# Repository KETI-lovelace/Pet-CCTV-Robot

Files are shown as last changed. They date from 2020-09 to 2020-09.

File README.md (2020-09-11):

# Pet-CCTV-Robot
2020 제4회 KETI 모비우스 개발자 대회 러브레이스 팀

## Overview
  직장인들의 외출에 펫을 감시하기 위한 펫 CCTV, 하지만 기존 펫 CCTV는 사용자가 앱으로 직접 스트리밍 영상을 보면서 반려동물의 상황을 파악 해야하기 때문에 용무가 있어 외출을 한 사용자들에게는 스트리밍 영상을 통한 감시를 할 수 없는 상황이 대부분이다. 또한, 터치를 통해 구동되는 가전제품들이 증가함으로 반려동물의 사고 또한 빈번히 발생한다. 예로 반려동물 주인이 외출시 반려동물이 인덕션, 하이라이트 전자레인지 등을 건드려서 화재가 발생했다는 사건이 급증했다. ([화재사건기사내용](https://www.hankyung.com/life/article/201912041776Y)) 우리는 이에대해 기존의 제품이 구매자의 목적을 완벽하게 해소시켜주지 못한다는 점과 현재 사고들의 원인을 파악하여 사용자가 위험구역을 지정하고, 반려동물의 위치를 자동적으로 파악하여 기존 펫 CCTV의 부족한 점을 보완하고자한다.
 
## 세부 기능
- 사용자가 직접 본 기기 카메라에서 송출하는 화면을 통해 전면, 좌측, 우측 방향에 반려동물이 접근하면 안되는 구역을 설정을 할 수 있다.
- 본 기기는 인공지능을 통해 전면, 좌측, 우측 방향으로 반려동물의 위치를 파악한다.
- 반려동물이 사용자가 지정한 접근 금지 구역에 위치했을 때 기기는 음성을 송출하여 반려동물에게 제지를 하고, 사용자의 앱에 알림을 울린다. ([소리를 통해 반려동물을 제지할 수 있을까?](https://youtu.be/sFJ1QNv7OGw?t=42))

## 순차적 동작 개념 설명
1.	카메라에서 송출하고 있는 영상이 터치 스크린에 출력이 되고, 모터를 통해 움직이는 카메라의 각도(0도, 90도, 180도)별로 원하는 위험구역을 스크린에 터치한다.
2.	위험 구역 설정을 마무리하면, 카메라에서 촬영되고 있는 영상을 앱에 실시간으로 전송한다.
3.	6초 간격으로 모터를 돌려 카메라의 위치를 바꾼다. (이때 해당 카메라 각도로 설정한 위험구역을 불러온다.)
4.	고양이 / 강아지를 탐지한다.
5.	탐지한 고양이/ 강아지의 위치가 사용자가 설정한 위험구역 내에 위치할 경우 스피커로 음성 송출 및 사용자 앱에 알림을 송신한다.

## 사용재료
  라즈베리 파이3B+, 라즈베리 파이4, 라즈베리파이 카메라 모듈*2, 180도 서보모터, 마이크로 SD카드 32G, SD카드 리더기, 라즈베리파이 공식7인치 터치스크린, 스피커 모듈, Coral USB accelerator

## 모델링 

모델은 [STL 파일](https://github.com/KETI-lovelace/Pet-CCTV-Robot/tree/master/hard%20case)로 첨부한다. 3D프린팅 편의를 위해 파트가 다음과 같이 분할되어 있다. 

```
hard case
 ├─camera_fixer.STL
 ├─camera_fixer_front.STL
 ├─cat_ear2.STL
 ├─cat_head_case.STL
 ├─cat_neck3.STL
 ├─cat_shape_behind2.STL
 ├─cat_shape_cap4.STL
 ├─cat_shape_side_wall3_back.STL
 ├─cat_shape_side_wall3_front.STL
 ├─head_behind.STL
 └─motor_case3.STL
```

위의 파트들을 모두 합쳐 에셈블을 만들면 다음과 같다.
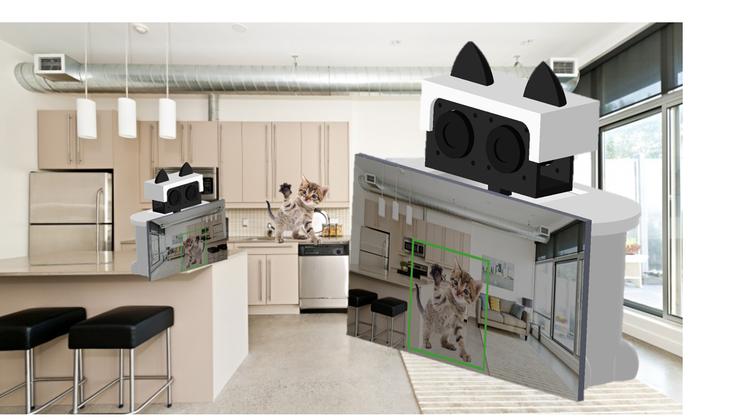
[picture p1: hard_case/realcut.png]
최종 모델


## 하드웨어 세부 구성
```
.
├── Google Edge TPU coprocessor : 인공지능 영상처리 가속화
├── raspberry pi 3 B+: 사용자에게 영상을 스트리밍 해줄 보드 
├── raspberry pi 4: 애완동물을 인식하여 위험구역을 탐지할 보드
├── HS-311 servo motor: 카메라를 돌려줄 모터
├── SONY pi camera x 2: 카메라(하나는 애완동물 인식, 하나는 스트리밍용)
├── raspberry pi touch screen 7 inch: 사용자가 상호작용할 터치디스플레이
└── USB port speaker: 음성을 출력할 스피커
```

## 반려동물 감지 (detection)
파이카메라로 받은 영상을 Tensorflow-Lite와 OpenCV, Google의  sample TFLite model을 이용하여 고양이, 강아지, 새 등의 애완동물을 인공지능으로 학습하여 인식 가능하게 만들었다. 파이카메라로 영상을 받으면, 처음에 터치스크린을 터치하여 화면 상의 위험 구역을 선정한다. 그러면 화면 상에 고양이, 강아지 등 반려동물이 보이면 인공지능이 인식을 하고, 사용자가 선정한 위험 구역 범위에 인식된 반려동물의 좌표값이 들어오면 반려동물의 행위를 저지하는 음성을 출력하고, 사용자의 앱으로 알림을 준다. 영상처리에서는 FPS를 개선하기 위해 TPU Accelerator를 사용하였으며, raspberry pi 3 B 에서 raspberry pi 4로 새로 교체하여 기존의 파이카메라로 영상처리를 할때 약 1에서 2 FPS였던 것을 약 30에서 40 FPS정도까지 끌어올려 부드러운 영상이 나오도록 했다. 
파일 실행 방법은 다음과 같다.
```
source tflite1-env/bin/activate
python3 TFLite_detection_webcam.py --modeldir=Sample_TFLite_model --edgetpu
```
## 애플리케이션
앱으로도 카메라의 영상이 스트리밍 될 수 있도록 하기 위해 UV4L/AWS를 사용하여 영상이 스트리밍 될 수 있도록 두가지 버전을 만들었다. UV4L을 이용할 경우, 스트리밍 하는 영상의 width, height, brightness, contrast, saturation, rgb balance, sharpness, rotate, jpeg quality, frame rate, horizontal mirror, vertical mirror, video denoise, image stabilization 등등 다양한 설정값을 변경하여 영상 스트리밍을 앱으로 받아볼 수 있다. <br>
### 주의사항
1. UV4L을 사용할 경우 : 라즈베리파이와 앱이 설치된 핸드폰이 반드시 같은 와이파이를 사용하고 있어야 영상 스트리밍 가능. 스트리밍 딜레이 거의 없음.
2. AWS를 사용할 경우 : 라즈베리파이와 앱이 설치된 핸드폰이 와이파이 사용 종류에 구애받지 않음. 인터넷 환경에 따라 스트리밍에서 1~10초의 딜레이 발생.

라즈베리 파이에서 인공지능으로 고양이, 강아지를 인식하여 사용자가 지정한 위험구역에 들어오면 앱으로 푸시알림을 보낸다. 사용자가 이름과 email 정보를 입력하면 반려동물이 위험구역에 접근했을 때 앱으로 알림이 가는 서비스를 구독할 수 있다. 구독자의 정보는 파이어베이스 데이터베이스에 실시간으로 반영되고, 구독 해지 시 자동으로 데이터베이스에서 정보를 삭제한다. 파이어베이스에서 사용자들의 정보와 사용량, 동시 연결 수, 클라우드 메시징(푸시알림)이 사용자에게 몇번 전송되고, 수신되고, 노출되고, 열렸는지를 실시간으로 모니터링할 수 있다. 또한 여러 대의 스마트폰 디바이스에서 실시간 스트리밍을 볼 수 있고, 푸시알림을 받을 수 있다.

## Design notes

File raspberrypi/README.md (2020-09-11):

# 라즈베리파이 내 프로그램 상세 설명

## 프로그램 세부 구성

1. [위험 구역 설정](https://github.com/KETI-lovelace/Pet-CCTV-Robot/tree/master/raspberrypi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)
2. [모터 회전](https://github.com/KETI-lovelace/Pet-CCTV-Robot/tree/master/raspberrypi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)
3. [반려동물 디텍팅](https://github.com/KETI-lovelace/Pet-CCTV-Robot/tree/master/raspberrypi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)
4. [소리 송출](https://github.com/KETI-lovelace/Pet-CCTV-Robot/tree/master/raspberrypi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)

## 1. 위험 구역 설정



### 코드부분
```python
while True:
    danger_frame = videostream.read()
    cv2.rectangle(danger_frame,(440,370),(540,410),(255,255,255),-1)
    cv2.putText(danger_frame,'NEXT'.format(frame_rate_calc),(450,400),cv2.FONT_HERSHEY_SIMPLEX,1,(50,50,255),2,cv2.LINE_AA)
    cv2.namedWindow('set_danger',cv2.WND_PROP_FULLSCREEN)
    cv2.setWindowProperty('set_danger',cv2.WND_PROP_FULLSCREEN,cv2.WINDOW_FULLSCREEN)
    cv2.imshow('set_danger', danger_frame)
    cv2.setMouseCallback('set_danger', mouse_callback)
    if(next_btn >  2): # 모든 위험구역 설정 완료
        next_btn = 2
        break
    k = cv2.waitKey(1)
    if k == 'd':
        break
cv2.destroyAllWindows()
```

### 상세 설명
- 좌측에서부터 카메라로부터 촬영되는 화면을 스크린을 통해 볼 수 있다.
- ``mousecallback`` 함수를 이용해 원하는 위험구역을 설정을 완료하고 ``NEXT`` 버튼을 누른다.
- 모터가 움직이며 우측,정면에서도 동일한 과정을 거친다.

## 2. 모터 구동

### 코드 부분

```python
# next_btn = 0 : 0 angle , = 1 : 90 angle , 2 = 180 angle

# motor angle change
pi = pigpio.pi()
pi.set_servo_pulsewidth(servoPin, 0) # turn off 18 pin connected servo motor.
pi.set_servo_pulsewidth(servoPin,800 * next_btn + 700)

# automatically change servomotor angle
while True:
    count += 1
    if( count > 180 ) :
        count = 0
        pi.set_servo_pulsewidth(servoPin,800 * next_btn + 700)
        if(is180):
            curr_btn = next_btn
            next_btn -= 1
        else:
            curr_btn = next_btn
            next_btn += 1
        if(next_btn == 2 or next_btn  == 0):
            is180 = not is180

...

```
### 상세 설명

- ``pigpio`` 모듈 사용
    - 원래는 ``ChangeDutyCycle`` 를 이용해 모터 각도를 전환시켰으나 떨림이 심해서, ``pigpio``선택
    - 설치 방법은 아래와 같다.

    ```bash
    $sudo apt-get update
    $sudo apt-get install pigpio python-pigpio python3-pigpio
    ```
    - 코드 작성 방법은 아래와 같다.

    ```python
    import pigpio

    from time import sleep
    
    pi = pigpio.pi() #먼저 사용할 pigpio.pi를 매칭해줍니다.
    while True:
        pi.set_servo_pulsewidth(18, 0) # 18번 채널에연결된 서보모터를 꺼줍니다. 
        sleep(1)
        pi.set_servo_pulsewidth(18, 700) # 18번채널에 연결된 서보모터를 0도로 이동
        sleep(1)
        pi.set_servo_pulsewidth(18, 1500) # 가운데로 이동 90도
        sleep(1)
        pi.set_servo_pulsewidth(18, 2300) # 180도 끝으로 이동. 
        sleep(1)
    ```
    - 실행 방법은 아래와 같다.

    ```bash
    $sudo pigpiod # pigpiod 실행
    $sudo python3 [파일 명]
    $sudo killall pigpiod # pigpiod 종료
    ```
- ``next_btn`` 이 0,1,2 일 때, 각각 0도, 90도 180도 표지를 의미한다.
- ``count``가 180 이상이되면, 모터 각도를 0도 -> 90도 -> 180도 -> 90도 -> 0도 순서대로 전환하는것을 반복한다.

## 3. 반려동물 디텍팅



- 라즈베리파이 반려동물 디텍팅에는 다음의 [오픈소스](https://github.com/EdjeElectronics/TensorFlow-Lite-Object-Detection-on-Android-and-Raspberry-Pi/blob/master/Raspberry_Pi_Guide.md)를 이용했다.

## 4. 소리 송출

### 코드 부분

```python
pygame.mixer.init()
music_file = "Dontgo.wav"
pygame.mixer.music.load(music_file)
pygame.mixer.music.play()
clock=pygame.time.Clock()
while pygame.mixer.music.get_busy():
    clock.tick(5)
```

### 상세 설명

- ``pygame`` 모듈 이용

## 5. 안드로이드 앱
Firebase로 안드로이드 앱에 알림을 보내는 부분으로, appalarm.py이다.<br>

### 코드 부분
```python
#3. 먼저 firebase database에서 저장된 token을 모두 가져와야 한다.
firebase = firebase.FirebaseApplication("https://soboro-6d610.firebaseio.com/", None)
result = firebase.get("/users", None)
listToken = []
for k, v in result.items():
    listToken.append(v["token"])
```
```python
push_service = FCMNotification(api_key="AAAACXndXcs:APA91bETtBU2UsGeSIToJYp4SFfx0VimIQthlDvZDQD5MmDAD0dCIqbl2JOevt0O0thLAJAGNb_rxkQzeuUYF51CkqO8O0Q_HVtP84TrrTnjE8nnuLJOLXHAHdsUepMfKH2szyw8YklQ")
```
이 부분에 본인의 FCMNotification api key를 입력한다. 확인 방법은 다음과 같다.<br>
Firebase 콘솔 접속 -> Settings -> 클라우드 메시징 -> 서버 키 부분의 토큰<br>
```python
message_title = "Soboro"
message_body = "Hurry up! Your pet is danger! Click this alarm!"
message_sound = "default"
```
이부분을 수정하여 푸시 알림의 타이틀, 내용, 소리 등을 바꿀 수 있다.<br>
<br>
appalarm.py는 TFLite_detection_webcam.py에서 쉡스크립트로 실행된다.<br>
```python
subprocess.call(['bash', 'runappalarm.sh'])
```
### 실행 전 설치 라이브러리
```
$sudo pip install pyfcm
```

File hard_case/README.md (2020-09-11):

## 하드케이스 모델링

### 연출 사진



### 구성

```
hard case
 ├─camera_fixer.STL
 ├─camera_fixer_front.STL
 ├─cat_ear2.STL
 ├─cat_head_case.STL
 ├─cat_neck3.STL
 ├─cat_shape_behind2.STL
 ├─cat_shape_cap4.STL
 ├─cat_shape_side_wall3_back.STL
 ├─cat_shape_side_wall3_front.STL
 ├─head_behind.STL
 └─motor_case3.STL
```

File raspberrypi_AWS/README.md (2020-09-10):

# AWS를 이용한 영상 스트리밍 상세 설명
이 파일을 영상 스트리밍을 할 라즈베리파이에 다운받고 AWS 스트리밍을 위해 다음과 같은 작업을 해줍니다.<br>
<br>

## 라즈베리파이에서 수행해줘야 할 작업
라즈베리파이에서 AWS 스트리밍을 실행하기 위해서는 이 레포지토리의 raspberrypi_AWS 폴더를 다운받은 뒤 다음과 같은 절차를 따릅니다.<br>
```
1. 라이브러리 설치
$ sudo apt-get install libgstreamer1.0-dev libgstreamer-plugins-base1.0-dev gstreamer1.0-plugins-base-apps gstreamer1.0-plugins-bad gstreamer1.0-plugins-good gstreamer1.0-plugins-ugly gstreamer1.0-tools

2. 환경변수 설정
$ export AWS_ACCESS_KEY_ID=YourAccessKeyId
$ export AWS_SECRET_ACCESS_KEY=YourSecretAccessKey

3. 종속 라이브러리 연결
$ cd /etc/ld.so.conf.d
$ sudo vim kinesis.conf
실행 파일이랑 같이 넘겨준 libKinesisProducer.so 등이 저장되어 있는 경로 입력
$ sudo ldconfig

4. 실행
$./KinesisStreaming.out <streaming name>
```
<br>
streaming name은 App_AWS에서 설정되어있는 arten입니다. 변경하려면 직접 안드로이드 스튜디오에서 코드를 수정하세요.

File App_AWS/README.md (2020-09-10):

# AWS를 이용한 영상 스트리밍 Android App 상세 설명
라즈베리파이에서 위험 구역에 반려 동물 진입 시 사용자 앱으로 알림을 전송합니다.<br>
앱 알림은 Firebase로 구현되어 있습니다.<br>
실시간 스트리밍 기능은 AWS로 구현되어 있습니다.<br>
이 앱을 실행시키기 위한 상세 작업은 다음과 같습니다. <br>
<br>

## 라즈베리파이에서 수행해줘야 할 작업
라즈베리파이에서 AWS 스트리밍을 실행하기 위해서는 이 레포지토리의 raspberrypi_AWS 폴더를 다운받은 뒤 다음과 같은 절차를 따릅니다.<br>
```
1. 라이브러리 설치
$ sudo apt-get install libgstreamer1.0-dev libgstreamer-plugins-base1.0-dev gstreamer1.0-plugins-base-apps gstreamer1.0-plugins-bad gstreamer1.0-plugins-good gstreamer1.0-plugins-ugly gstreamer1.0-tools

2. 환경변수 설정
$ export AWS_ACCESS_KEY_ID=YourAccessKeyId
$ export AWS_SECRET_ACCESS_KEY=YourSecretAccessKey

3. 종속 라이브러리 연결
$ cd /etc/ld.so.conf.d
$ sudo vim kinesis.conf
실행 파일이랑 같이 넘겨준 libKinesisProducer.so 등이 저장되어 있는 경로 입력
$ sudo ldconfig

4. 실행
$./KinesisStreaming.out <streaming name>
```
<br>

## 안드로이드 스튜디오에서 수행해줘야 할 작업
```
private String accessKeyId = "";
private String secretKey = "";
```
이부분에 AWS 계정에서 생성한 accessKeyId와 secretKey를 입력합니다.<br>
코드 상에서는 보안 문제로 빈칸 처리해두었습니다.<br>
주의!! 앱 내에 AWS 키를 넣은 채로 깃에 푸시하면 안됩니다. 보안 문제로 메일이 쇄도할겁니다.<br>
위의 라즈베리파이에서 수행해줘야 할 작업에서 4번 부분의 <streaming name>은 앱의 AWSManager의 37번째 줄의 arten을 사용하면 됩니다.<br>
<br>

## 구독 정보 관리
이름, 이메일을 입력하고 "알림을 받겠습니다"를 체크 후, "구독합니다"버튼을 누르면 실시간 알림이 앱으로 전송됩니다.<br>
"해지합니다"버튼을 누르면 실시간 알림 기능이 취소됩니다.<br>
구독을 누른 사용자의 데이터는 Firebase 콘솔의 RealtimeDatabase를 통해 확인할 수 있습니다.<br>
만약 앱 알림이 제대로 오지 않는다면, Firebase 콘솔에서 해당 사용자의 token이 제대로 발급되었는지 확인해보세요.<br>

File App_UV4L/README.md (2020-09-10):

# UV4L을 이용한 영상 스트리밍 Android App 상세 설명
라즈베리파이에서 위험 구역에 반려 동물 진입 시 사용자 앱으로 알림을 전송합니다.<br>
앱 알림은 Firebase로 구현되어 있습니다.<br>
실시간 스트리밍 기능은 UV4L로 구현되어 있습니다.<br>
이 앱을 실행시키기 위한 상세 작업은 다음과 같습니다. <br>
<br>

## 라즈베리파이에서 수행해줘야 할 작업
라즈베리파이에서 UV4L 스트리밍을 실행하기 위해서는 이 레포지토리의 raspberrypi 폴더를 다운받은 뒤 다음과 같은 절차를 따릅니다.<br>
```
$ sudo service uv4l_raspicam restart (서비스 실행하기)
```
UV4L이 실행되면, 웹브라우저로 http://192.168.137.150:8080/ 에 접속합니다.<br>
Settings에서 픽셀을 가로 : 320, 세로 : 256로 맞춰줍니다. 안드로이드 앱 내에서 적절한 화면 크기를 유지하기 위해서입니다.<br>
MJPEGStills stream을 누르면 웹브라우저에서 파이캠의 영상 스트리밍이 시작됩니다.<br>
실행중인 프로세스를 죽일때는 다음과 같은 명령어를 사용합니다.<br>
```
pkill uv4l
```
<br>

## 안드로이드 스튜디오에서 수행해줘야 할 작업
```
webView.loadUrl("http://라즈베리파이의ip:8080/stream");
```
이부분에 본인의 라즈베리파이의 ip주소를 쓴 뒤 빌드합니다.<br>
라즈베리파이의 ip주소는 ifconfig로 확인할 수 있습니다.<br>
<br>

## 구독 정보 관리
이름, 이메일을 입력하고 "알림을 받겠습니다"를 체크 후, "구독합니다"버튼을 누르면 실시간 알림이 앱으로 전송됩니다.<br>
"해지합니다"버튼을 누르면 실시간 알림 기능이 취소됩니다.<br>
구독을 누른 사용자의 데이터는 Firebase 콘솔의 RealtimeDatabase를 통해 확인할 수 있습니다.<br>
만약 앱 알림이 제대로 오지 않는다면, Firebase 콘솔에서 해당 사용자의 token이 제대로 발급되었는지 확인해보세요.<br>

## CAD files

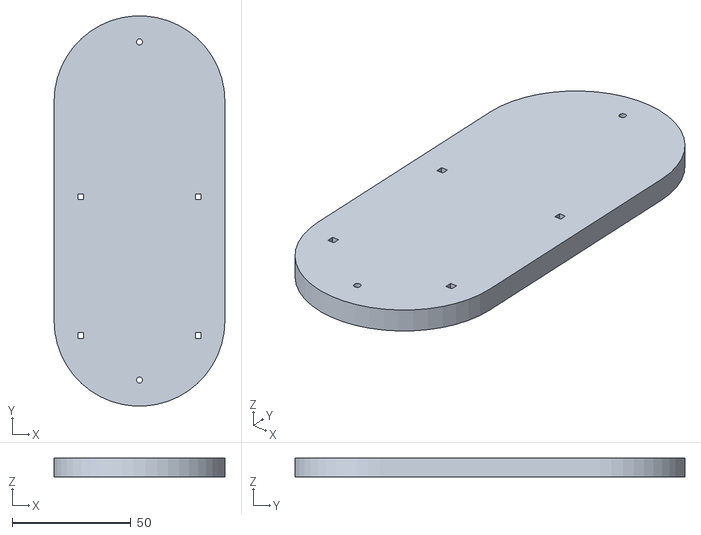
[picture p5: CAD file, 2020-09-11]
hard_case/cat_shape_behind2.STL
72.0 x 164.3 x 8.00

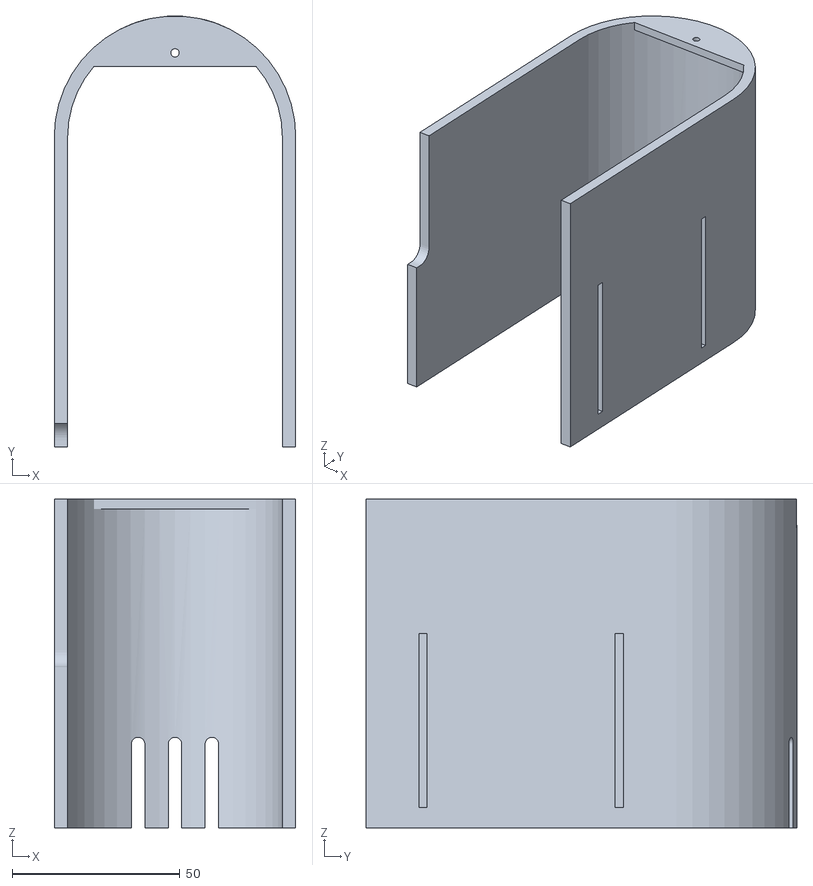
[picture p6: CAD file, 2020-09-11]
hard_case/cat_shape_side_wall3_back.STL
72.0 x 128.5 x 98.0

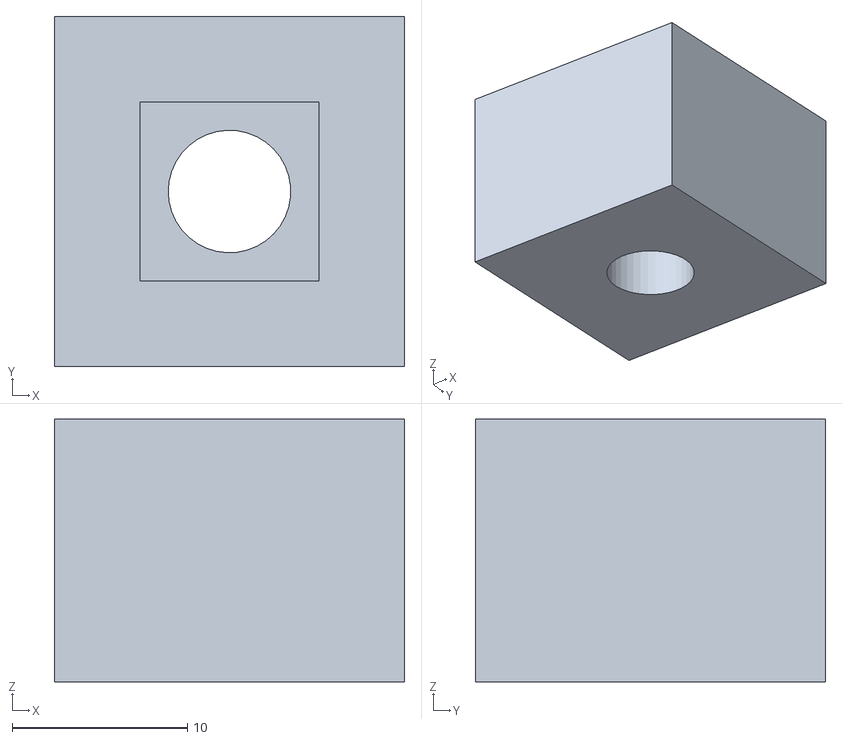
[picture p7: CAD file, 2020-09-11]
hard_case/cat_neck3.STL
20.0 x 20.0 x 15.0

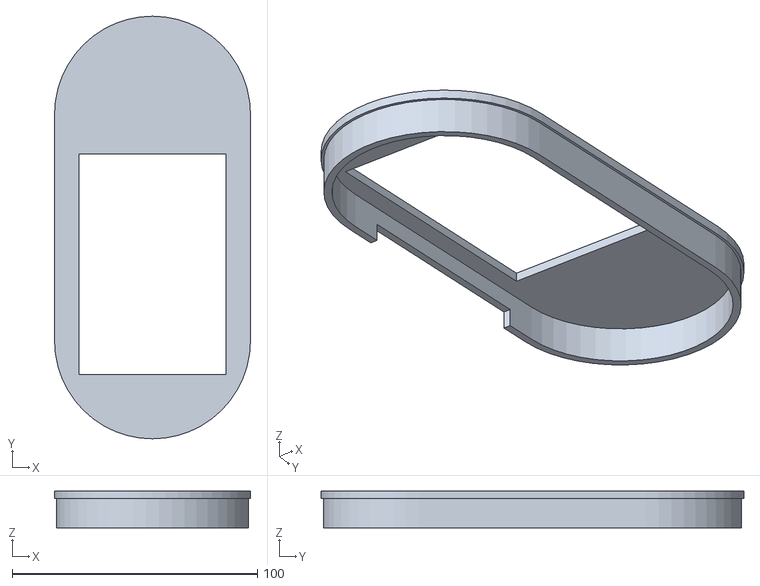
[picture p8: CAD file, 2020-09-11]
hard_case/cat_shape_cap4.STL
80.0 x 172.5 x 15.0

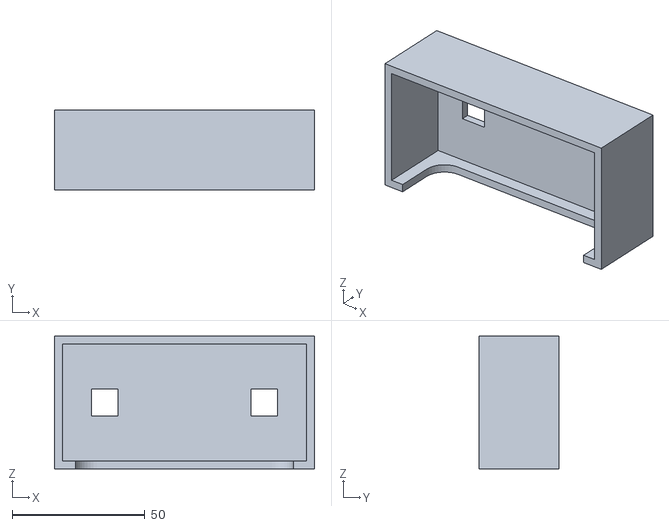
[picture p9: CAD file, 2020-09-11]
hard_case/cat_head_case.STL
98.0 x 30.0 x 50.0

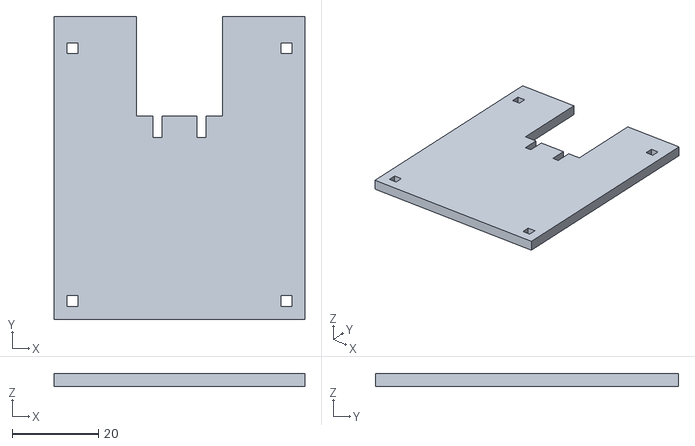
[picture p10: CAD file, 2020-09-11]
hard_case/motor_case3.STL
58.0 x 70.1 x 3.00

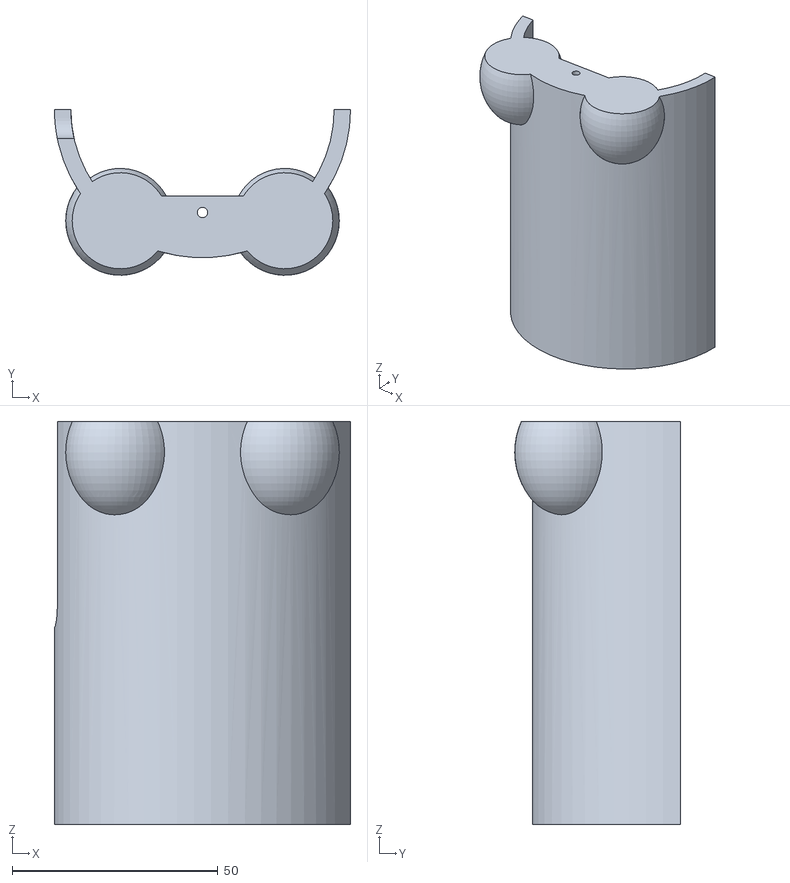
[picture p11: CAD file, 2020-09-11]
hard_case/cat_shape_side_wall3_front.STL
72.0 x 40.3 x 98.0

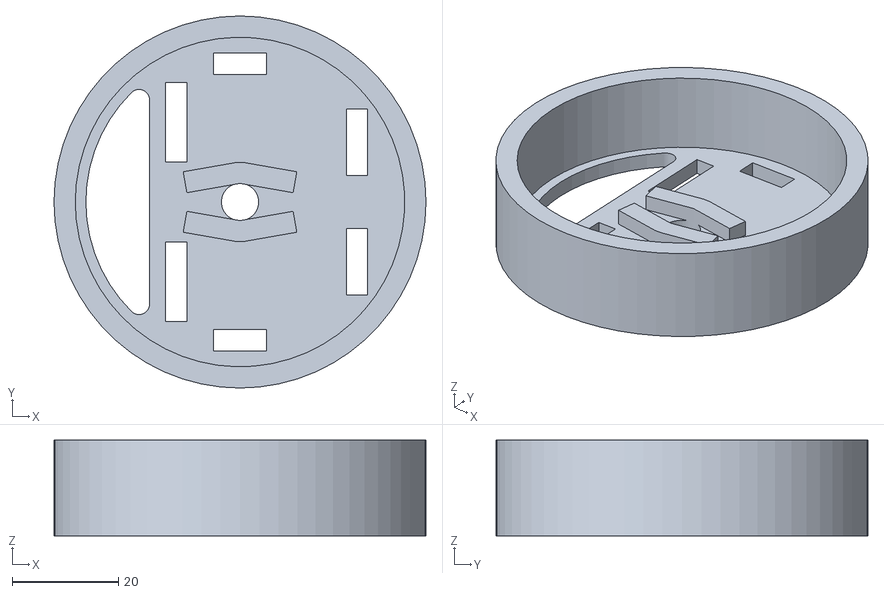
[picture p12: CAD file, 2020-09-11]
hard_case/head_behind.STL
70.0 x 70.0 x 18.0

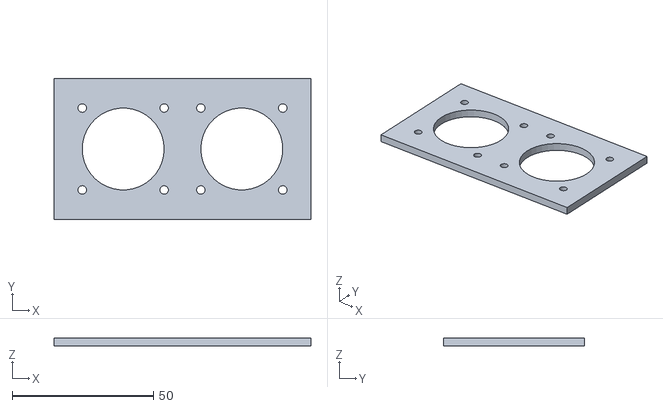
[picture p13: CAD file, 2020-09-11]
hard_case/camera_fixer.STL
91.0 x 50.0 x 3.00

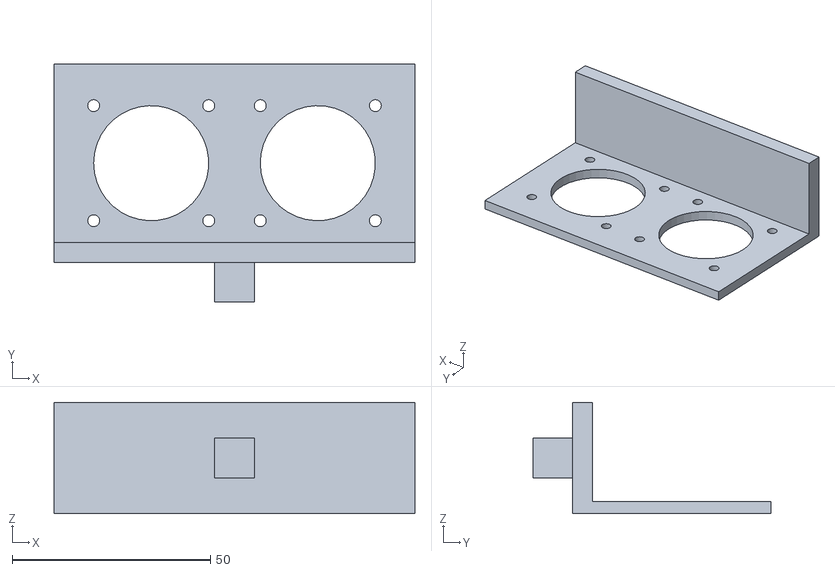
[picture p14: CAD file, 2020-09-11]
hard_case/camera_fixer_front.STL
91.0 x 60.0 x 28.0

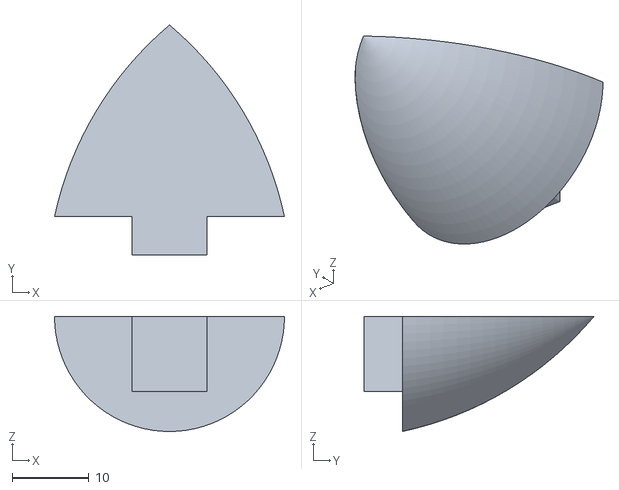
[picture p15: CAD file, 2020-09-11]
hard_case/cat_ear2.STL
30.0 x 30.0 x 15.0

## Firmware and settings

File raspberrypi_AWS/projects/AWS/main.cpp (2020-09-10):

//#include <gst/gst.h>
//#include <gst/app/gstappsink.h>
//#include <string.h>
//#include <chrono>
//#include <vector>
//#include <stdlib.h>
//#include <mutex>
//#include <credential-providers/IotCertCredentialProvider.h>
//#include <KinesisVideoProducer.h>
//
//using namespace std;
//using namespace com::amazonaws::kinesis::video;
//
//#ifdef __cplusplus
//extern "C" {
//#endif
//
//    int gstreamer_init(int, char**);
//
//#ifdef __cplusplus
//}
//#endif
//
//#define DEFAULT_RETENTION_PERIOD_HOURS 2
//#define DEFAULT_KMS_KEY_ID ""
//#define DEFAULT_STREAMING_TYPE STREAMING_TYPE_REALTIME
//#define DEFAULT_CONTENT_TYPE "video/h264"
//#define DEFAULT_MAX_LATENCY_SECONDS 60
//#define DEFAULT_FRAGMENT_DURATION_MILLISECONDS 2000
//#define DEFAULT_TIMECODE_SCALE_MILLISECONDS 1
//#define DEFAULT_KEY_FRAME_FRAGMENTATION TRUE
//#define DEFAULT_FRAME_TIMECODES TRUE
//#define DEFAULT_ABSOLUTE_FRAGMENT_TIMES TRUE
//#define DEFAULT_FRAGMENT_ACKS TRUE
//#define DEFAULT_RESTART_ON_ERROR TRUE
//#define DEFAULT_RECALCULATE_METRICS TRUE
//#define DEFAULT_STREAM_FRAMERATE 25
//#define DEFAULT_AVG_BANDWIDTH_BPS (4 * 1024 * 1024)
//#define DEFAULT_BUFFER_DURATION_SECONDS 120
//#define DEFAULT_REPLAY_DURATION_SECONDS 40
//#define DEFAULT_CONNECTION_STALENESS_SECONDS 60
//#define DEFAULT_CODEC_ID "V_MPEG4/ISO/AVC"
//#define DEFAULT_TRACKNAME "kinesis_video"
//#define DEFAULT_FRAME_DURATION_MS 1
//#define DEFAULT_CREDENTIAL_ROTATION_SECONDS 3600
//#define DEFAULT_CREDENTIAL_EXPIRATION_SECONDS 180
//
//typedef enum _StreamSource {
//    FILE_SOURCE,
//    LIVE_SOURCE,
//    RTSP_SOURCE
//} StreamSource;
//
//typedef struct _FileInfo {
//    _FileInfo() :
//        path(""),
//        last_fragment_ts(0) {}
//    string path;
//    uint64_t last_fragment_ts;
//} FileInfo;
//
//typedef struct _CustomData {
//
//    _CustomData() :
//        streamSource(LIVE_SOURCE),
//        h264_stream_supported(false),
//        synthetic_dts(0),
//        last_unpersisted_file_idx(0),
//        stream_status(STATUS_SUCCESS),
//        base_pts(0),
//        max_frame_pts(0),
//        key_frame_pts(0),
//        main_loop(NULL),
//        first_pts(GST_CLOCK_TIME_NONE),
//        use_absolute_fragment_times(true) {
//        producer_start_time = chrono::duration_cast<nanoseconds>(systemCurrentTime().time_since_epoch()).count();
//    }
//
//    GMainLoop* main_loop;
//    unique_ptr<KinesisVideoProducer> kinesis_video_producer;
//    shared_ptr<KinesisVideoStream> kinesis_video_stream;
//    bool stream_started;
//    bool h264_stream_supported;
//    char* stream_name;
//    mutex file_list_mtx;
//
//    // list of files to upload.
//    vector<FileInfo> file_list;
//
//    // index of file in file_list that application is currently trying to upload.
//    uint32_t current_file_idx;
//
//    // index of last file in file_list that haven't been persisted.
//    atomic_uint last_unpersisted_file_idx;
//
//    // stores any error status code reported by StreamErrorCallback.
//    atomic_uint stream_status;
//
//    // Since each file's timestamp start at 0, need to add all subsequent file's timestamp to base_pts starting from the
//    // second file to avoid fragment overlapping. When starting a new putMedia session, this should be set to 0.
//    // Unit: ns
//    uint64_t base_pts;
//
//    // Max pts in a file. This will be added to the base_pts for the next file. When starting a new putMedia session,
//    // this should be set to 0.
//    // Unit: ns
//    uint64_t max_frame_pts;
//
//    // When uploading file, store the pts of frames that has flag FRAME_FLAG_KEY_FRAME. When the entire file has been uploaded,
//    // key_frame_pts contains the timetamp of the last fragment in the file. key_frame_pts is then stored into last_fragment_ts
//    // of the file.
//    // Unit: ns
//    uint64_t key_frame_pts;
//
//    // Used in file uploading only. Assuming frame timestamp are relative. Add producer_start_time to each frame's
//    // timestamp to convert them to absolute timestamp. This way fragments dont overlap after token rotation when doing
//    // file uploading.
//    uint64_t producer_start_time;
//
//    volatile StreamSource streamSource;
//
//    string rtsp_url;
//
//    unique_ptr<Credentials> credential;
//
//    uint64_t synthetic_dts;
//
//    bool use_absolute_fragment_times;
//
//    // Pts of first video frame
//    uint64_t first_pts;
//} CustomData;
//
//namespace com {
//    namespace amazonaws {
//        namespace kinesis {
//            namespace video {
//
//                class SampleClientCallbackProvider : public ClientCallbackProvider {
//                public:
//
//                    UINT64 getCallbackCustomData() override {
//                        return reinterpret_cast<UINT64> (this);
//                    }
//
//                    StorageOverflowPressureFunc getStorageOverflowPressureCallback() override {
//                        return storageOverflowPressure;
//                    }
//
//                    static STATUS storageOverflowPressure(UINT64 custom_handle, UINT64 remaining_bytes);
//                };
//
//                class SampleStreamCallbackProvider : public StreamCallbackProvider {
//                    UINT64 custom_data_;
//                public:
//                    SampleStreamCallbackProvider(UINT64 custom_data) : custom_data_(custom_data) {}
//
//                    UINT64 getCallbackCustomData() override {
//                        return custom_data_;
//                    }
//
//                    StreamConnectionStaleFunc getStreamConnectionStaleCallback() override {
//                        return streamConnectionStaleHandler;
//                    };
//
//                    StreamErrorReportFunc getStreamErrorReportCallback() override {
//                        return streamErrorReportHandler;
//                    };
//
//                    DroppedFrameReportFunc getDroppedFrameReportCallback() override {
//                        return droppedFrameReportHandler;
//                    };
//
//                    FragmentAckReceivedFunc getFragmentAckReceivedCallback() override {
//                        return fragmentAckReceivedHandler;
//                    };
//
//                private:
//                    static STATUS
//                        streamConnectionStaleHandler(UINT64 custom_data, STREAM_HANDLE stream_handle,
//                            UINT64 last_buffering_ack);
//
//                    static STATUS
//                        streamErrorReportHandler(UINT64 custom_data, STREAM_HANDLE stream_handle, UPLOAD_HANDLE upload_handle, UINT64 errored_timecode,
//                            STATUS status_code);
//
//                    static STATUS
//                        droppedFrameReportHandler(UINT64 custom_data, STREAM_HANDLE stream_handle,
//                            UINT64 dropped_frame_timecode);
//
//                    static STATUS
//                        fragmentAckReceivedHandler(UINT64 custom_data, STREAM_HANDLE stream_handle,
//                            UPLOAD_HANDLE upload_handle, PFragmentAck pFragmentAck);
//                };
//
//                class SampleCredentialProvider : public StaticCredentialProvider {
//                    // Test rotation period is 40 second for the grace period.
//                    const std::chrono::duration<uint64_t> ROTATION_PERIOD = std::chrono::seconds(DEFAULT_CREDENTIAL_ROTATION_SECONDS);
//                public:
//                    SampleCredentialProvider(const Credentials& credentials) :
//                        StaticCredentialProvider(credentials) {}
//
//                    void updateCredentials(Credentials& credentials) override {
//                        // Copy the stored creds forward
//                        credentials = credentials_;
//
//                        // Update only the expiration
//                        auto now_time = std::chrono::duration_cast<std::chrono::seconds>(
//                            systemCurrentTime().time_since_epoch());
//                        auto expiration_seconds = now_time + ROTATION_PERIOD;
//                        credentials.setExpiration(std::chrono::seconds(expiration_seconds.count()));
//                    }
//                };
//
//                class SampleDeviceInfoProvider : public DefaultDeviceInfoProvider {
//                public:
//                    device_info_t getDeviceInfo() override {
//                        auto device_info = DefaultDeviceInfoProvider::getDeviceInfo();
//                        // Set the storage size to 128mb
//                        device_info.storageInfo.storageSize = 128 * 1024 * 1024;
//                        return device_info;
//                    }
//                };
//
//                STATUS
//                    SampleClientCallbackProvider::storageOverflowPressure(UINT64 custom_handle, UINT64 remaining_bytes) {
//                    UNUSED_PARAM(custom_handle);
//                    return STATUS_SUCCESS;
//                }
//
//                STATUS SampleStreamCallbackProvider::streamConnectionStaleHandler(UINT64 custom_data,
//                    STREAM_HANDLE stream_handle,
//                    UINT64 last_buffering_ack) {
//                    return STATUS_SUCCESS;
//                }
//
//                STATUS
//                    SampleStreamCallbackProvider::streamErrorReportHandler(UINT64 custom_data, STREAM_HANDLE stream_handle,
//                        UPLOAD_HANDLE upload_handle, UINT64 errored_timecode, STATUS status_code) {
//                    CustomData* data = reinterpret_cast<CustomData*>(custom_data);
//                    bool terminate_pipeline = false;
//
//                    // Terminate pipeline if error is not retriable or if error is retriable but we are streaming file.
//                    // When streaming file, we choose to terminate the pipeline on error because the easiest way to recover
//                    // is to stream the file from the beginning again.
//                    // In realtime streaming, retriable error can be handled underneath. Otherwise terminate pipeline
//                    // and store error status if error is fatal.
//                    if ((IS_RETRIABLE_ERROR(status_code) && data->streamSource == FILE_SOURCE) ||
//                        (!IS_RETRIABLE_ERROR(status_code) && !IS_RECOVERABLE_ERROR(status_code))) {
//                        data->stream_status = status_code;
//                        terminate_pipeline = true;
//                    }
//
//                    if (terminate_pipeline && data->main_loop != NULL) {
//                        g_main_loop_quit(data->main_loop);
//                    }
//
//                    return STATUS_SUCCESS;
//                }
//
//                STATUS
//                    SampleStreamCallbackProvider::droppedFrameReportHandler(UINT64 custom_data, STREAM_HANDLE stream_handle,
//                        UINT64 dropped_frame_timecode) {
//                    return STATUS_SUCCESS;
//                }
//
//                STATUS
//                    SampleStreamCallbackProvider::fragmentAckReceivedHandler(UINT64 custom_data, STREAM_HANDLE stream_handle,
//                        UPLOAD_HANDLE upload_handle, PFragmentAck pFragmentAck) {
//                    CustomData* data = reinterpret_cast<CustomData*>(custom_data);
//                    if (data->streamSource == FILE_SOURCE && pFragmentAck->ackType == FRAGMENT_ACK_TYPE_PERSISTED) {
//                        std::unique_lock<std::mutex> lk(data->file_list_mtx);
//                        uint32_t last_unpersisted_file_idx = data->last_unpersisted_file_idx.load();
//                        uint64_t last_frag_ts = data->file_list.at(last_unpersisted_file_idx).last_fragment_ts /
//                            duration_cast<nanoseconds>(milliseconds(DEFAULT_TIMECODE_SCALE_MILLISECONDS)).count();
//                        if (last_frag_ts != 0 && last_frag_ts == pFragmentAck->timestamp) {
//                            data->last_unpersisted_file_idx = last_unpersisted_file_idx + 1;
//                        }
//                    }
//                    return STATUS_SUCCESS;
//                }
//
//            }  // namespace video
//        }  // namespace kinesis
//    }  // namespace amazonaws
//}  // namespace com;
//
//static void eos_cb(GstElement* sink, CustomData* data) {
//    // bookkeeping base_pts. add 1ms to avoid overlap.
//    data->base_pts += +data->max_frame_pts + duration_cast<nanoseconds>(milliseconds(1)).count();
//    data->max_frame_pts = 0;
//
//    {
//        std::unique_lock<std::mutex> lk(data->file_list_mtx);
//        // store file's last fragment's timestamp.
//        data->file_list.at(data->current_file_idx).last_fragment_ts = data->key_frame_pts;
//    }
//
//    g_main_loop_quit(data->main_loop);
//}
//
//void create_kinesis_video_frame(Frame* frame, const nanoseconds& pts, const nanoseconds& dts, FRAME_FLAGS flags,
//    void* data, size_t len) {
//    frame->flags = flags;
//    frame->decodingTs = static_cast<UINT64>(dts.count()) / DEFAULT_TIME_UNIT_IN_NANOS;
//    frame->presentationTs = static_cast<UINT64>(pts.count()) / DEFAULT_TIME_UNIT_IN_NANOS;
//    // set duration to 0 due to potential high spew from rtsp streams
//    frame->duration = 0;
//    frame->size = static_cast<UINT32>(len);
//    frame->frameData = reinterpret_cast<PBYTE>(data);
//    frame->trackId = DEFAULT_TRACK_ID;
//}
//
//bool put_frame(shared_ptr<KinesisVideoStream> kinesis_video_stream, void* data, size_t len, const nanoseconds& pts, const nanoseconds& dts, FRAME_FLAGS flags) {
//    Frame frame;
//    create_kinesis_video_frame(&frame, pts, dts, flags, data, len);
//    return kinesis_video_stream->putFrame(frame);
//}
//
//static GstFlowReturn on_new_sample(GstElement* sink, CustomData* data) {
//    GstBuffer* buffer;
//    bool isDroppable, isHeader, delta;
//    size_t buffer_size;
//    GstFlowReturn ret = GST_FLOW_OK;
//    STATUS curr_stream_status = data->stream_status.load();
//    GstSample* sample = nullptr;
//    GstMapInfo info;
//
//    if (STATUS_FAILED(curr_stream_status)) {
//        ret = GST_FLOW_ERROR;
//        goto CleanUp;
//    }
//
//    info.data = nullptr;
//    sample = gst_app_sink_pull_sample(GST_APP_SINK(sink));
//
//    // capture cpd at the first frame
//    if (!data->stream_started) {
//        data->stream_started = true;
//        GstCaps* gstcaps = (GstCaps*)gst_sample_get_caps(sample);
//        GstStructure* gststructforcaps = gst_caps_get_structure(gstcaps, 0);
//        const GValue* gstStreamFormat = gst_structure_get_value(gststructforcaps, "codec_data");
//        gchar* cpd = gst_value_serialize(gstStreamFormat);
//        data->kinesis_video_stream->start(std::string(cpd));
//        g_free(cpd);
//    }
//
//    buffer = gst_sample_get_buffer(sample);
//    isHeader = GST_BUFFER_FLAG_IS_SET(buffer, GST_BUFFER_FLAG_HEADER);
//    isDroppable = GST_BUFFER_FLAG_IS_SET(buffer, GST_BUFFER_FLAG_CORRUPTED) ||
//        GST_BUFFER_FLAG_IS_SET(buffer, GST_BUFFER_FLAG_DECODE_ONLY) ||
//        (GST_BUFFER_FLAGS(buffer) == GST_BUFFER_FLAG_DISCONT) ||
//        (GST_BUFFER_FLAG_IS_SET(buffer, GST_BUFFER_FLAG_DISCONT) && GST_BUFFER_FLAG_IS_SET(buffer, GST_BUFFER_FLAG_DELTA_UNIT)) ||
//        // drop if buffer contains header only and has invalid timestamp
//        (isHeader && (!GST_BUFFER_PTS_IS_VALID(buffer) || !GST_BUFFER_DTS_IS_VALID(buffer)));
//
//    if (!isDroppable) {
//
//        delta = GST_BUFFER_FLAG_IS_SET(buffer, GST_BUFFER_FLAG_DELTA_UNIT);
//
//        FRAME_FLAGS kinesis_video_flags = delta ? FRAME_FLAG_NONE : FRAME_FLAG_KEY_FRAME;
//
//        // Always synthesize dts for file sources because file sources dont have meaningful dts.
//        // For some rtsp sources the dts is invalid, therefore synthesize.
//        if (data->streamSource == FILE_SOURCE || !GST_BUFFER_DTS_IS_VALID(buffer)) {
//            data->synthetic_dts += DEFAULT_FRAME_DURATION_MS * HUNDREDS_OF_NANOS_IN_A_MILLISECOND * DEFAULT_TIME_UNIT_IN_NANOS;
//            buffer->dts = data->synthetic_dts;
//        }
//        else if (GST_BUFFER_DTS_IS_VALID(buffer)) {
//            data->synthetic_dts = buffer->dts;
//        }
//
//        if (data->streamSource == FILE_SOURCE) {
//            data->max_frame_pts = MAX(data->max_frame_pts, buffer->pts);
//
//            // make sure the timestamp is continuous across multiple files.
//            buffer->pts += data->base_pts + data->producer_start_time;
//
//            if (CHECK_FRAME_FLAG_KEY_FRAME(kinesis_video_flags)) {
//                data->key_frame_pts = buffer->pts;
//            }
//        }
//        else if (data->use_absolute_fragment_times) {
//            if (data->first_pts == GST_CLOCK_TIME_NONE) {
//                data->first_pts = buffer->pts;
//            }
//            buffer->pts += data->producer_start_time - data->first_pts;
//        }
//
//        if (!gst_buffer_map(buffer, &info, GST_MAP_READ)) {
//            goto CleanUp;
//        }
//
//        put_frame(data->kinesis_video_stream, info.data, info.size, std::chrono::nanoseconds(buffer->pts),
//            std::chrono::nanoseconds(buffer->dts), kinesis_video_flags);
//    }
//
//CleanUp:
//
//    if (info.data != nullptr) {
//        gst_buffer_unmap(buffer, &info);
//    }
//
//    if (sample != nullptr) {
//        gst_sample_unref(sample);
//    }
//
//    return ret;
//}
//
//static bool format_supported_by_source(GstCaps* src_caps, GstCaps* query_caps, int width, int height, int framerate) {
//    gst_caps_set_simple(query_caps,
//        "width", G_TYPE_INT, width,
//        "height", G_TYPE_INT, height,
//        "framerate", GST_TYPE_FRACTION, framerate, 1,
//        NULL);
//    bool is_match = gst_caps_can_intersect(query_caps, src_caps);
//
//    // in case the camera has fps as 10000000/333333
//    if (!is_match) {
//        gst_caps_set_simple(query_caps,
//            "framerate", GST_TYPE_FRACTION_RANGE, framerate, 1, framerate + 1, 1,
//            NULL);
//        is_match = gst_caps_can_intersect(query_caps, src_caps);
//    }
//
//    return is_match;
//}
//
//static bool resolution_supported(GstCaps* src_caps, GstCaps* query_caps_raw, GstCaps* query_caps_h264,
//    CustomData& data, int width, int height, int framerate) {
//    if (query_caps_h264 && format_supported_by_source(src_caps, query_caps_h264, width, height, framerate)) {
//        data.h264_stream_supported = true;
//    }
//    else if (query_caps_raw && format_supported_by_source(src_caps, query_caps_raw, width, height, framerate)) {
//        data.h264_stream_supported = false;
//    }
//    else {
//        return false;
//    }
//    return true;
//}
//
///* This function is called when an error message is posted on the bus */
//static void error_cb(GstBus* bus, GstMessage* msg, CustomData* data) {
//    GError* err;
//    gchar* debug_info;
//
//    /* Print error details on the screen */
//    gst_message_parse_error(msg, &err, &debug_info);
//    g_printerr("Error received from element %s: %s\n", GST_OBJECT_NAME(msg->src), err->message);
//    g_printerr("Debugging information: %s\n", debug_info ? debug_info : "none");
//    g_clear_error(&err);
//    g_free(debug_info);
//
//    g_main_loop_quit(data->main_loop);
//}
//
//void kinesis_video_init(CustomData* data) {
//    unique_ptr<DeviceInfoProvider> device_info_provider(new SampleDeviceInfoProvider());
//    unique_ptr<ClientCallbackProvider> client_callback_provider(new SampleClientCallbackProvider());
//    unique_ptr<StreamCallbackProvider> stream_callback_provider(new SampleStreamCallbackProvider(
//        reinterpret_cast<UINT64>(data)));
//
//    char const* accessKey;
//    char const* secretKey;
//    char const* sessionToken;
//    char const* defaultRegion;
//    string defaultRegionStr;
//    string sessionTokenStr;
//
//    char const* iot_get_credential_endpoint;
//    char const* cert_path;
//    char const* private_key_path;
//    char const* role_alias;
//    char const* ca_cert_path;
//
//    unique_ptr<CredentialProvider> credential_provider;
//
//    printf("another\n");
//
//    if (nullptr == (defaultRegion = getenv(DEFAULT_REGION_ENV_VAR))) {
//        defaultRegionStr = DEFAULT_AWS_REGION;
//    }
//    else {
//        defaultRegionStr = string(defaultRegion);
//    }
//    printf("Using region: %s\n", defaultRegionStr);
//
//    if (nullptr != (accessKey = getenv(ACCESS_KEY_ENV_VAR)) &&
//        nullptr != (secretKey = getenv(SECRET_KEY_ENV_VAR))) {
//
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
//int main (int argc, char* argv[]) {
//
//    if (argc < 2) {
//        printf("nope\n");
//        return 1;
//    }
//
//    printf("go\n");
//
//    const int PUTFRAME_FAILURE_RETRY_COUNT = 3;
//
//    CustomData data;
//    char stream_name[MAX_STREAM_NAME_LEN + 1];
//    int ret = 0;
//    int file_retry_count = PUTFRAME_FAILURE_RETRY_COUNT;
//    STATUS stream_status = STATUS_SUCCESS;
//
//    STRNCPY(stream_name, argv[1], MAX_STREAM_NAME_LEN);
//    stream_name[MAX_STREAM_NAME_LEN] = '\0';
//    data.stream_name = stream_name;
//
//    printf("go\n");
//
//    data.streamSource = LIVE_SOURCE;
//
//    /* init Kinesis Video */
//    try {
//        kinesis_video_init(&data);
//        printf("go\n");
//        kinesis_video_stream_init(&data);
//    }
//    catch (runtime_error& err) {
//        printf("error occured\n %s\n", err.what());
//        return 1;
//    }
//
//    printf("go\n");
//
//    bool do_retry = true;
//
//    // non file uploading scenario
//    gstreamer_init(argc, argv, &data);
//    if (STATUS_SUCCEEDED(stream_status)) {
//        // if stream_status is success after eos, send out remaining frames.
//        data.kinesis_video_stream->stopSync();
//    }
//    else {
//        data.kinesis_video_stream->stop();
//    }
//
//    // CleanUp
//    data.kinesis_video_producer->freeStream(data.kinesis_video_stream);
//
//    return 0;
//}

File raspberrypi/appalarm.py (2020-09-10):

#-*- coding:utf-8 -*-
#한글때문에 python3으로 실행
#그러나 지원안되는 라이브러리 때문에 다시 python2로 변경 멘붕!

import json
import requests
#import pyrebase #python3 only
from firebase import firebase
from  pyfcm import FCMNotification #python2 only
#from pusher import Pusher #python2 only
import sys


#한글에러 해결
reload(sys)
sys.setdefaultencoding('utf8')


cSky = "1"
grade = "2"
myvalue = "3"
cTemp = "4"
cWind = "5"


####FCM 알림 보내기(이거 쓰레드로 처리해야 하나? 일단 이렇게 하자.)#### 
#3. 먼저 firebase database에서 저장된 token을 모두 가져와야 한다.
firebase = firebase.FirebaseApplication("https://soboro-6d610.firebaseio.com/", None)
result = firebase.get("/users", None)
listToken = []
for k, v in result.items():
    listToken.append(v["token"])
#    break
#print(listToken)
#k ,v = result.items()
#listToken.append(v["token"])


#4.sending message with pyfcm
push_service = FCMNotification(api_key="AAAACXndXcs:APA91bETtBU2UsGeSIToJYp4SFfx0VimIQthlDvZDQD5MmDAD0dCIqbl2JOevt0O0thLAJAGNb_rxkQzeuUYF51CkqO8O0Q_HVtP84TrrTnjE8nnuLJOLXHAHdsUepMfKH2szyw8YklQ")

#data_message
data_message = {
	"message_body":"날씨: "+cSky+", 미세먼지: "+grade+"("+myvalue+")",
	"하늘":cSky,
	"온도":cTemp,
	"풍속":cWind
}

# Send to multiple devices by passing a list of ids.
registration_ids = listToken #["token1", "token2", ....]
message_title = "Soboro"
message_body = "Hurry up! Your pet is danger! Click this alarm!"
message_sound = "default"
#display message
result = push_service.notify_multiple_devices(registration_ids=registration_ids, message_title=message_title, message_body=message_body)
#data_message payload
#result = push_service.notify_multiple_devices(registration_ids=registration_ids, message_title=message_title, message_body=message_body, data_message=data_message)
#data_message payload, without message_body #- 이렇게 data_message만 보내면 앱이 백그라운드일때도 앱에서 알림을 핸들링 한다.

result = push_service.notify_multiple_devices(registration_ids=registration_ids, data_message=data_message)

#result = push_service.single_device_data_message(registration_id=registration_ids[0], data_message=data_message)




# print result

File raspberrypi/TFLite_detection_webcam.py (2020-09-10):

# Import packages
import os
import argparse
import cv2
import numpy as np
import sys
import time
from threading import Thread
import importlib.util
import serial
import subprocess
from pyautogui import press,typewrite,hotkey
import pygame
import time
import RPi.GPIO as GPIO
import pigpio

# Define VideoStream class to handle streaming of video from webcam in separate processing thread
# Source - Adrian Rosebrock, PyImageSearch: https://www.pyimagesearch.com/2015/12/28/increasing-raspberry-pi-fps-with-python-and-opencv/
class VideoStream:
    """Camera object that controls video streaming from the Picamera"""
    def __init__(self,resolution=(640,480),framerate=30):
        # 640 , 480
        # Initialize the PiCamera and the camera image stream
        self.stream = cv2.VideoCapture(0)
        ret = self.stream.set(cv2.CAP_PROP_FOURCC, cv2.VideoWriter_fourcc(*'MJPG'))
        ret = self.stream.set(3,resolution[0])
        ret = self.stream.set(4,resolution[1])
            
        # Read first frame from the stream
        (self.grabbed, self.frame) = self.stream.read()

	# Variable to control when the camera is stopped
        self.stopped = False

    def start(self):
	# Start the thread that reads frames from the video stream
        Thread(target=self.update,args=()).start()
        return self

    def update(self):
        # Keep looping indefinitely until the thread is stopped
        while True:
            # If the camera is stopped, stop the thread
            if self.stopped:
                # Close camera resources
                self.stream.release()
                return

            # Otherwise, grab the next frame from the stream
            (self.grabbed, self.frame) = self.stream.read()

    def read(self):
	# Return the most recent frame
        return self.frame

    def stop(self):
	# Indicate that the camera and thread should be stopped
        self.stopped = True
# set mouse event
mouse_event_types = { 0:"EVENT_MOUSEMOVE", 1:"EVENT_LBUTTONDOWN", 2:"EVENT_RBUTTONDOWN", 3:"EVENT_MBUTTONDOWN",
                 4:"EVENT_LBUTTONUP", 5:"EVENT_RBUTTONUP", 6:"EVENT_MBUTTONUP",
                 7:"EVENT_LBUTTONDBLCLK", 8:"EVENT_RBUTTONDBLCLK", 9:"EVENT_MBUTTONDBLCLK",
                 10:"EVENT_MOUSEWHEEL", 11:"EVENT_MOUSEHWHEEL"}

mouse_event_flags = { 0:"None", 1:"EVENT_FLAG_LBUTTON", 2:"EVENT_FLAG_RBUTTON", 4:"EVENT_FLAG_MBUTTON",
                8:"EVENT_FLAG_CTRLKEY", 9:"EVENT_FLAG_CTRLKEY + EVENT_FLAG_LBUTTON",
                10:"EVENT_FLAG_CTRLKEY + EVENT_FLAG_RBUTTON", 11:"EVENT_FLAG_CTRLKEY + EVENT_FLAG_MBUTTON",

                16:"EVENT_FLAG_SHIFTKEY", 17:"EVENT_FLAG_SHIFTKEY + EVENT_FLAG_LBUTTON",
                18:"EVENT_FLAG_SHIFTLKEY + EVENT_FLAG_RBUTTON", 19:"EVENT_FLAG_SHIFTKEY + EVENT_FLAG_MBUTTON",

                32:"EVENT_FLAG_ALTKEY", 33:"EVENT_FLAG_ALTKEY + EVENT_FLAG_LBUTTON",
                34:"EVENT_FLAG_ALTKEY + EVENT_FLAG_RBUTTON", 35:"EVENT_FLAG_ALTKEY + EVENT_FLAG_MBUTTON"}

#ser = serial.Serial('/dev/ttyACM0',115200)
#ser.write(bytes('3',encoding='ascii'))

# Define and parse input arguments
parser = argparse.ArgumentParser()
parser.add_argument('--modeldir', help='Folder the .tflite file is located in',
                    required=True)
parser.add_argument('--graph', help='Name of the .tflite file, if different than detect.tflite',
                    default='detect.tflite')
parser.add_argument('--labels', help='Name of the labelmap file, if different than labelmap.txt',
                    default='labelmap.txt')
parser.add_argument('--threshold', help='Minimum confidence threshold for displaying detected objects',
                    default=0.5)
parser.add_argument('--resolution', help='Desired webcam resolution in WxH. If the webcam does not support the resolution entered, errors may occur.',
                    default='640x480')
parser.add_argument('--edgetpu', help='Use Coral Edge TPU Accelerator to speed up detection',
                    action='store_true')

args = parser.parse_args()

MODEL_NAME = args.modeldir
GRAPH_NAME = args.graph
LABELMAP_NAME = args.labels
min_conf_threshold = float(args.threshold)
resW, resH = args.resolution.split('x')
imW, imH = int(resW), int(resH)
use_TPU = args.edgetpu

# motor variables
servoPin = 18
SERVO_MAX_DUTY = 11
SERVO_MIN_DUTY = 3


# Import TensorFlow libraries
# If tflite_runtime is installed, import interpreter from tflite_runtime, else import from regular tensorflow
# If using Coral Edge TPU, import the load_delegate library
pkg = importlib.util.find_spec('tflite_runtime')
if pkg:
    from tflite_runtime.interpreter import Interpreter
    if use_TPU:
        from tflite_runtime.interpreter import load_delegate
else:
    from tensorflow.lite.python.interpreter import Interpreter
    if use_TPU:
        from tensorflow.lite.python.interpreter import load_delegate

# If using Edge TPU, assign filename for Edge TPU model
if use_TPU:
    # If user has specified the name of the .tflite file, use that name, otherwise use default 'edgetpu.tflite'
    if (GRAPH_NAME == 'detect.tflite'):
        GRAPH_NAME = 'edgetpu.tflite'       

# Get path to current working directory
CWD_PATH = os.getcwd()

# Path to .tflite file, which contains the model that is used for object detection
PATH_TO_CKPT = os.path.join(CWD_PATH,MODEL_NAME,GRAPH_NAME)

# Path to label map file
PATH_TO_LABELS = os.path.join(CWD_PATH,MODEL_NAME,LABELMAP_NAME)

# Load the label map
with open(PATH_TO_LABELS, 'r') as f:
    labels = [line.strip() for line in f.readlines()]

# Have to do a weird fix for label map if using the COCO "starter model" from
# https://www.tensorflow.org/lite/models/object_detection/overview
# First label is '???', which has to be removed.
if labels[0] == '???':
    del(labels[0])

# Load the Tensorflow Lite model.
# If using Edge TPU, use special load_delegate argument
if use_TPU:
    interpreter = Interpreter(model_path=PATH_TO_CKPT,
                              experimental_delegates=[load_delegate('libedgetpu.so.1.0')])
    print(PATH_TO_CKPT)
else:
    interpreter = Interpreter(model_path=PATH_TO_CKPT)

interpreter.allocate_tensors()

# Get model details
input_details = interpreter.get_input_details()
output_details = interpreter.get_output_details()
height = input_details[0]['shape'][1]
width = input_details[0]['shape'][2]

floating_model = (input_details[0]['dtype'] == np.float32)

input_mean = 127.5
input_std = 127.5

# Initialize frame rate calculation
frame_rate_calc = 1
freq = cv2.getTickFrequency()

# Initialize video stream
videostream = VideoStream(resolution=(imW,imH),framerate=30).start()
time.sleep(1)
# click event
next_btn = 0
# next_btn = 0 : 0 angle , = 1 : 90 angle , 2 = 180 angle 
danger_done = 0
set_danger_box = [[],[],[]]
# motor angle change
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

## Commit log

2020-08-18 라파이 파일 옮김
2020-09-10 upload raspberrypi
2020-09-10 upload raspberrypi for AWS
2020-09-11 add modeling
    [camera_fixer.STL, camera_fixer_front.STL, cat_ear2.STL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]
